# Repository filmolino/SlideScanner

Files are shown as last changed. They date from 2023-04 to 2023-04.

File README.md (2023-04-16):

# Filmolino SlideScanner
The Filmolino SlideScanner is a device that makes it easy to scan slides in magazines fully automated using a modified slide projector and a digital camera. It controls the slide projector and a digital camera using a cable release or an infrared remote control (Nikon, Canon, Pentax, Sony, Olympus, Minolta). New cable releases and IR controls can easyily be added to the software. 
 
Thanks to the [M5StampC3 from M5Stack](https://shop.m5stack.com/collections/m5-controllers/products/fire-iot-development-kit) using a ESP-32 core together with 16M Flash, 8M PSRAM and a built in 3.7V/500mAh Lithium battery it is also possible to use the device without a power supply and remote control the SlideScanner through a web interface over WiFi. The scanner has it's own access point to which you can connect.

The Filmolino SlideScanner is completely open source, so you can easy build your own!

For more info about the project please visit [Filmolino SlideScanner](https://filmolino.com/slidescanner/)

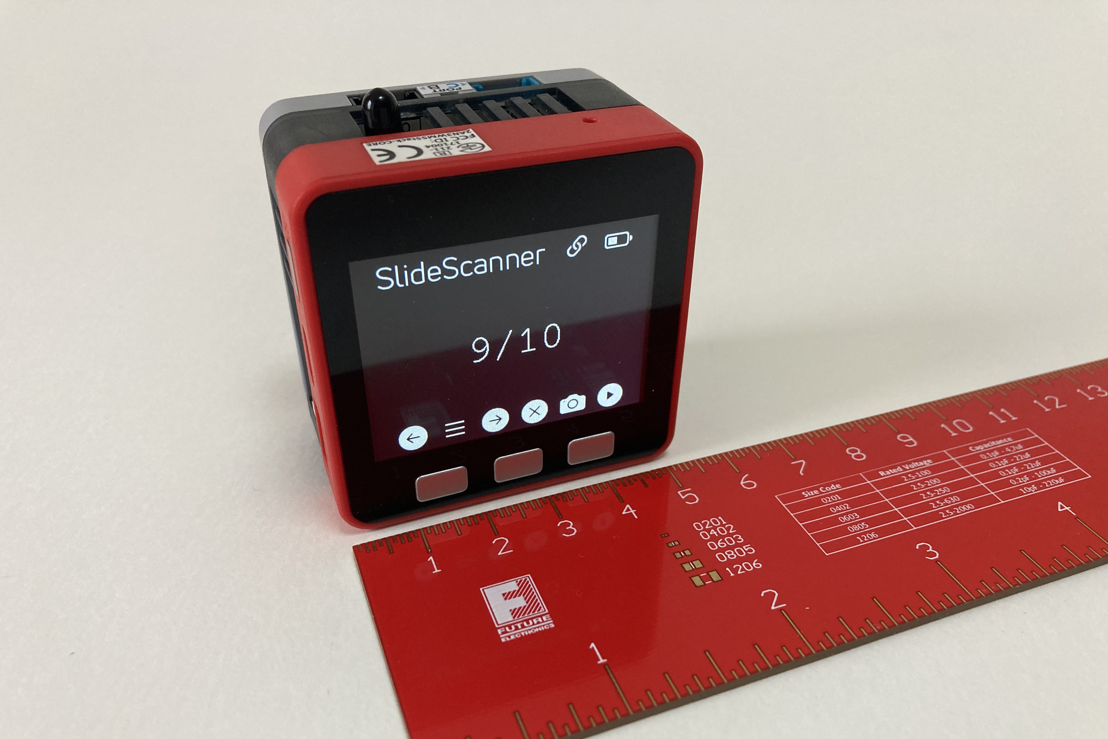
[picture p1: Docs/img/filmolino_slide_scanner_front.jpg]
Front view Front view Filmolino SlideScanner

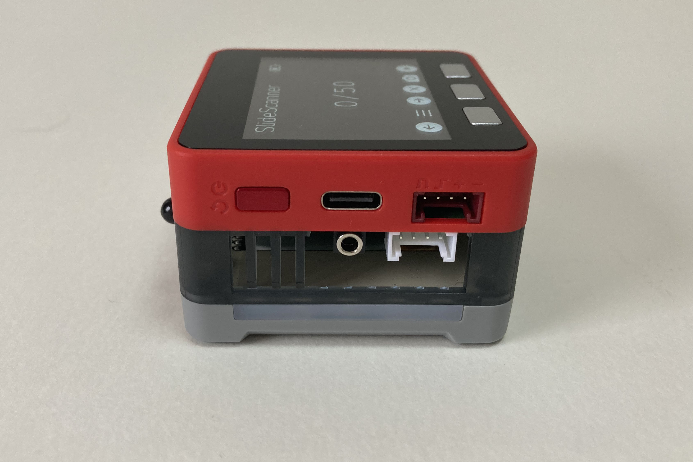
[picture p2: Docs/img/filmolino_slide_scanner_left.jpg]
Left view Left view Filmolino SlideScanner

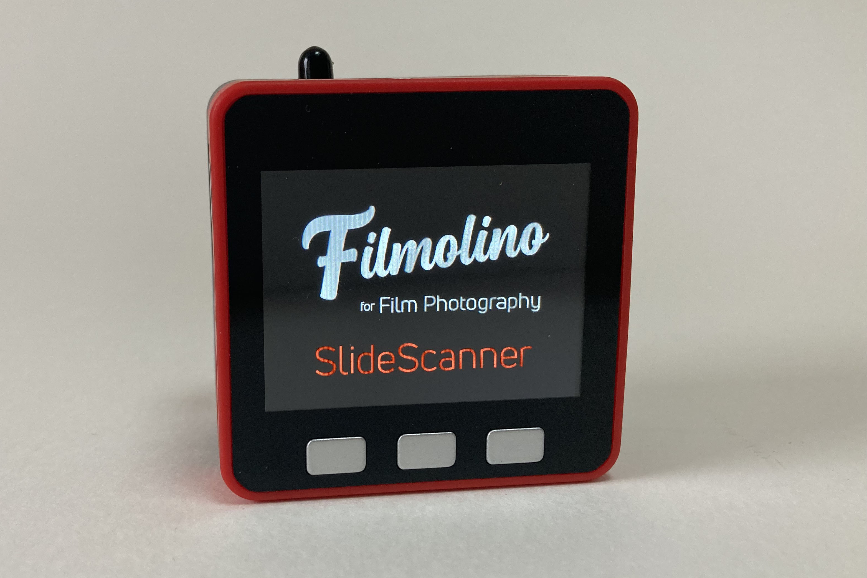
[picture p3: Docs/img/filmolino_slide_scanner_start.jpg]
Left view Left view Filmolino SlideScanner

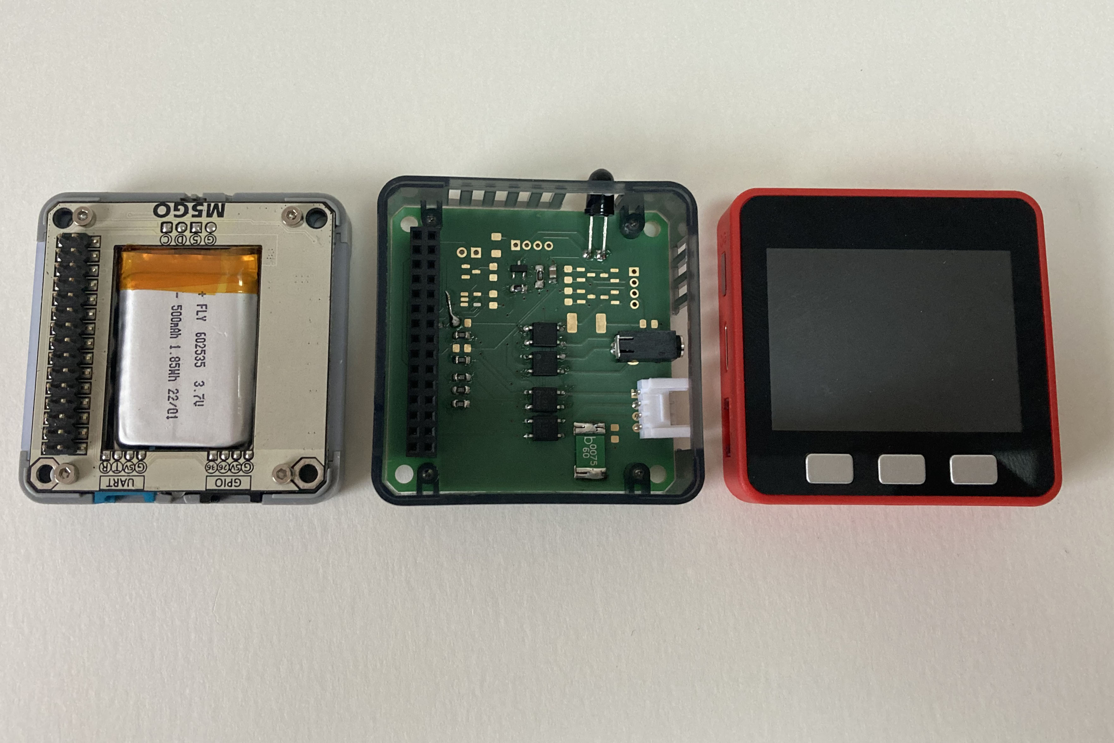
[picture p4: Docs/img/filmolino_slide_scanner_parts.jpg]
Parts view Parts


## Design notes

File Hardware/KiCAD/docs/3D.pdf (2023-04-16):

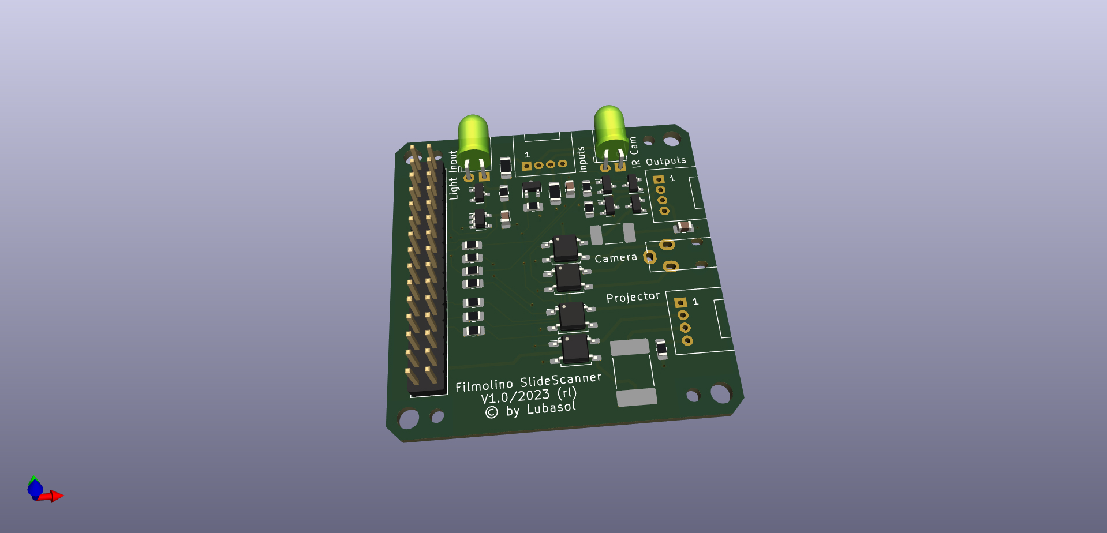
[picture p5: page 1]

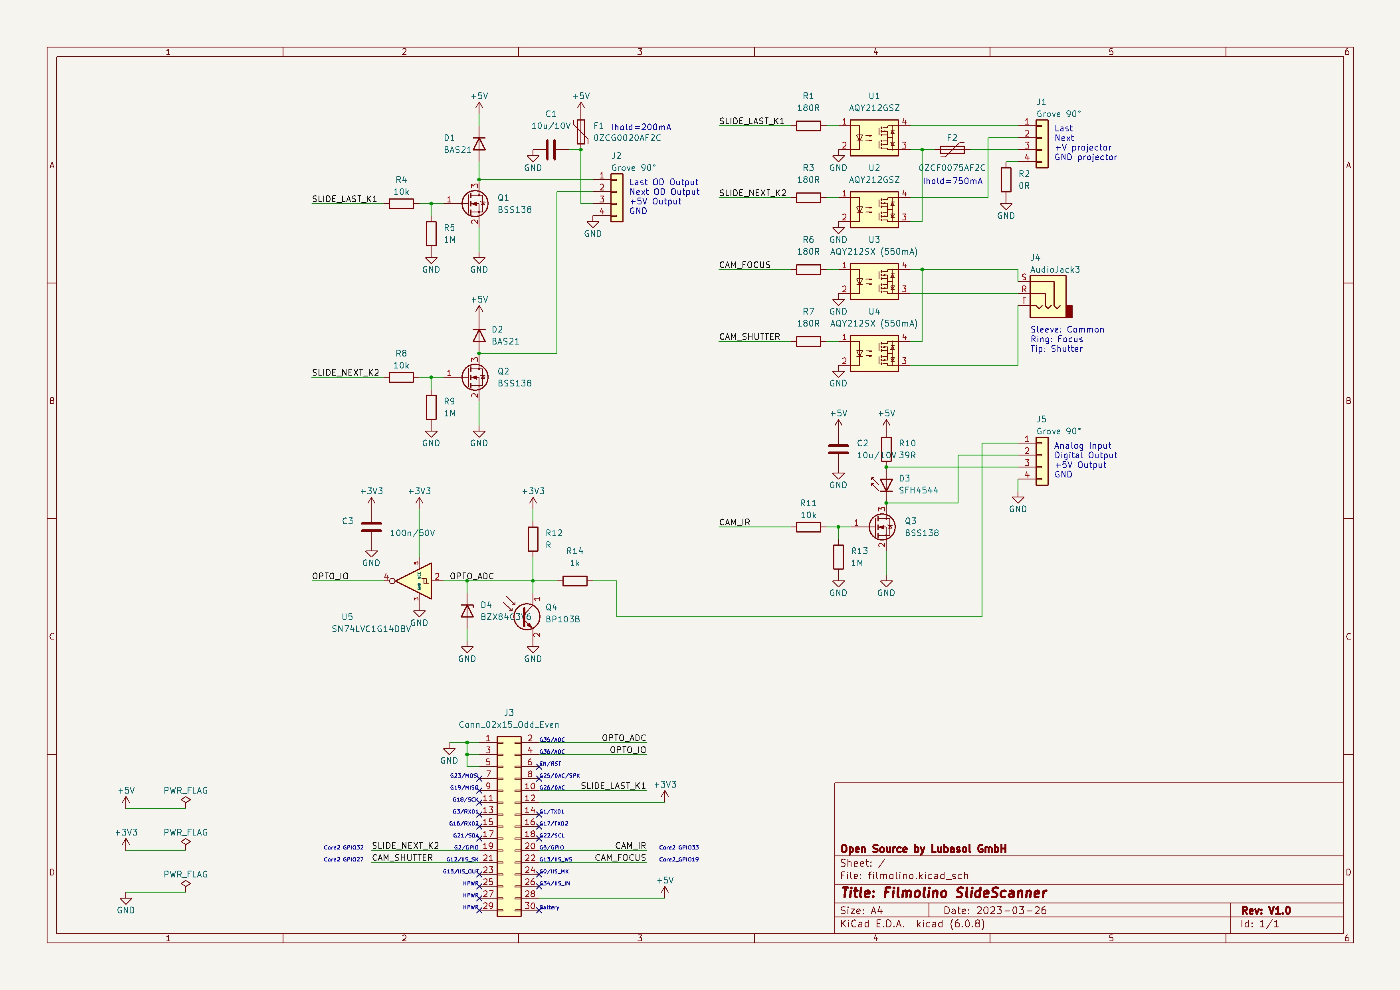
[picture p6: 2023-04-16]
Docs/img/kicad_schematic.jpg

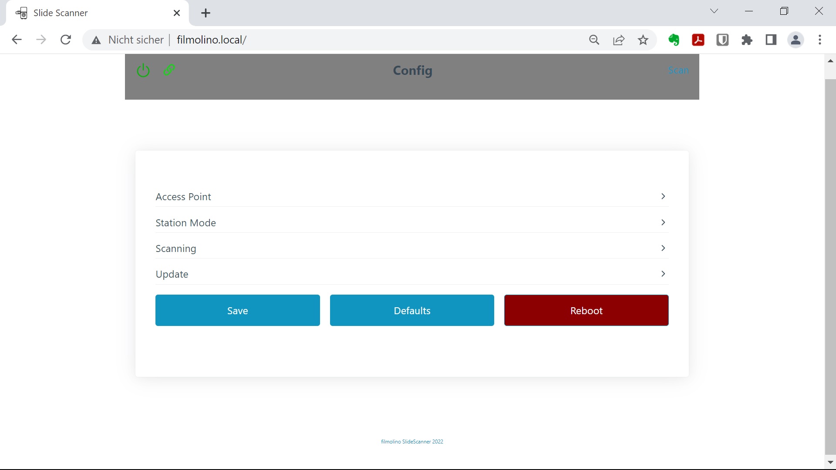
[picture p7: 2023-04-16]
Docs/img/web_config.jpg

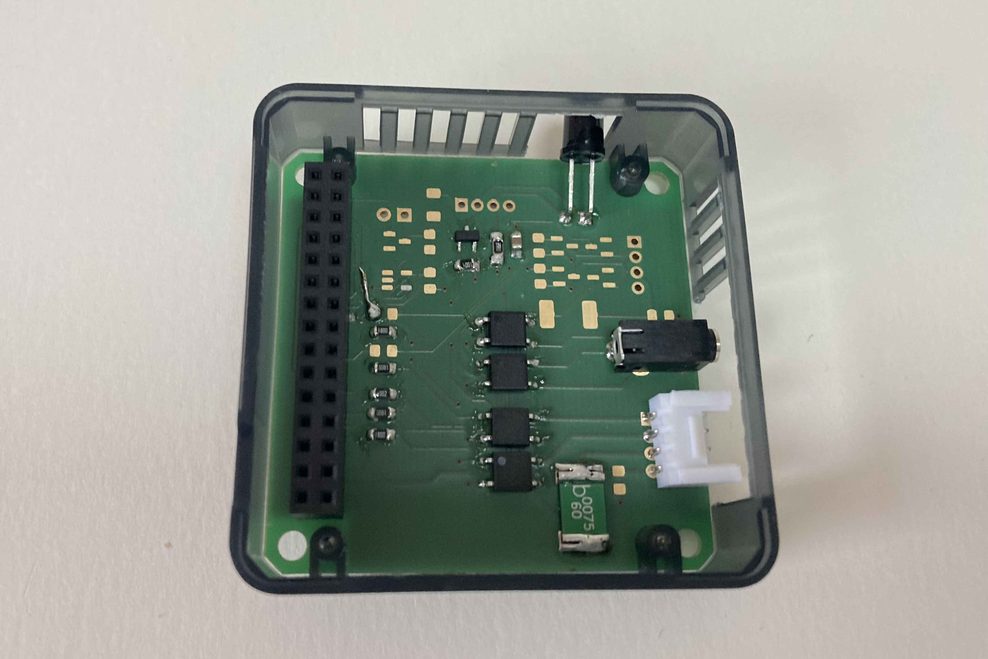
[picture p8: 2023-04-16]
Docs/img/filmolino_slide_scanner_pcb.jpg

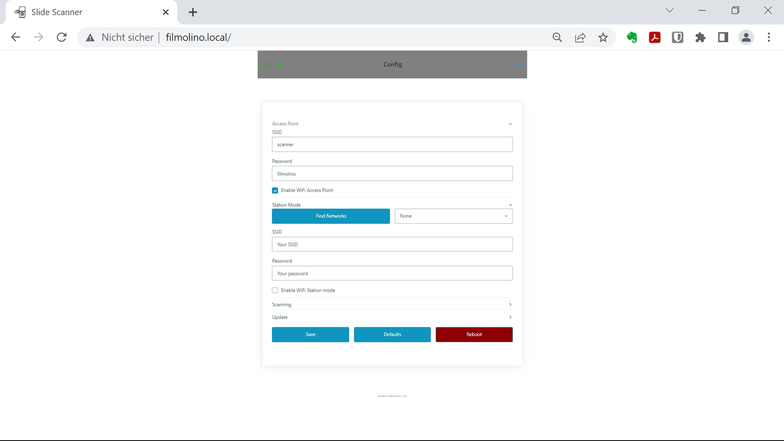
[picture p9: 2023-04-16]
Docs/img/web_config_wifi.jpg

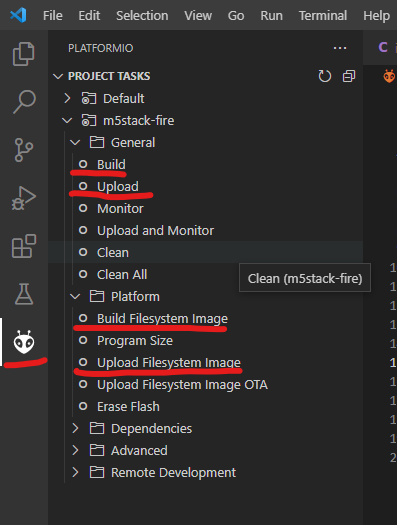
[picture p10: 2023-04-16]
Docs/img/platformio.png

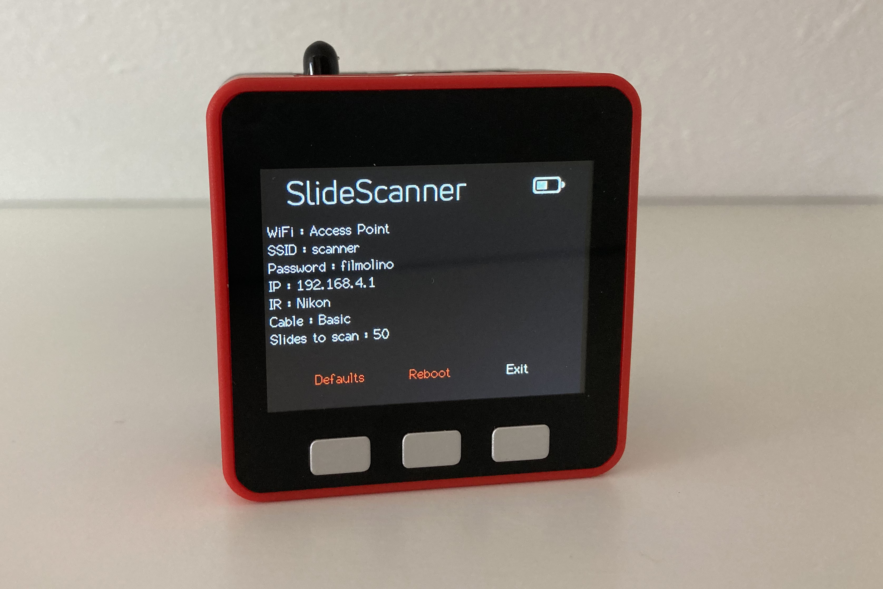
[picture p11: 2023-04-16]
Docs/img/filmolino_slide_scanner_config.jpg

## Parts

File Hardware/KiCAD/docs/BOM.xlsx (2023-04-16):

Id | Designator | Package | Quantity | Designation | Supplier and ref
1 | Q3,Q1,Q2 | SOT-23 | 3 | BSS138
2 | D1,D2 | SOT-23 | 2 | BAS21
3 | U3,U4 | SOP-4_4.4x4.3mm_P2.54mm | 2 | AQY212SX (550mA)
4 | U2,U1 | SOP-4_4.4x4.3mm_P2.54mm | 2 | AQY212GSZ
5 | R9,R5,R13 | R_0805_2012Metric_Pad1.20x1.40mm_HandSolder | 3 | 1M
6 | F1 | BelFuse_0ZCG_Metric_Pad1.78x3.50mm | 1 | 0ZCG0020AF2C
7 | R12 | R_0805_2012Metric_Pad1.20x1.40mm_HandSolder | 1 | R
8 | J4 | Jack_2.5mm_Lumberg_1501_04 | 1 | AudioJack3
9 | D4 | SOT-23 | 1 | BZX84C3V6
10 | J2,J1,J5 | Grove_Con_1x04_2mm_horizontal | 3 | Grove 90Â°
11 | J3 | PinHeader_2x15_P2.54mm_Holes0.75mm_Vertical | 1 | Conn_02x15_Odd_Even
12 | U5 | SOT-23-5 | 1 | SN74LVC1G14DBV
13 | R4,R11,R8 | R_0805_2012Metric_Pad1.20x1.40mm_HandSolder | 3 | 10k
14 | C2,C1 | C_0805_2012Metric_Pad1.18x1.45mm_HandSolder | 2 | 10u/10V
15 | D3 | LED_D5.0mm_Horizontal_O1.27mm_Z3.0mm | 1 | SFH4544
16 | F2 | BelFuse_0ZCF_Metric_Pad2.30x5.60mm | 1 | 0ZCF0075AF2C
17 | R1,R7,R3,R6 | R_0805_2012Metric_Pad1.20x1.40mm_HandSolder | 4 | 180R
18 | R2 | R_0805_2012Metric_Pad1.20x1.40mm_HandSolder | 1 | 0R
19 | Q4 | LED_D5.0mm_Horizontal_O1.27mm_Z3.0mm | 1 | BP103B
20 | C3 | C_0805_2012Metric_Pad1.18x1.45mm_HandSolder | 1 | 100n/50V
21 | R14 | R_1206_3216Metric_Pad1.30x1.75mm_HandSolder | 1 | 1k
22 | R10 | R_1206_3216Metric_Pad1.30x1.75mm_HandSolder | 1 | 39R

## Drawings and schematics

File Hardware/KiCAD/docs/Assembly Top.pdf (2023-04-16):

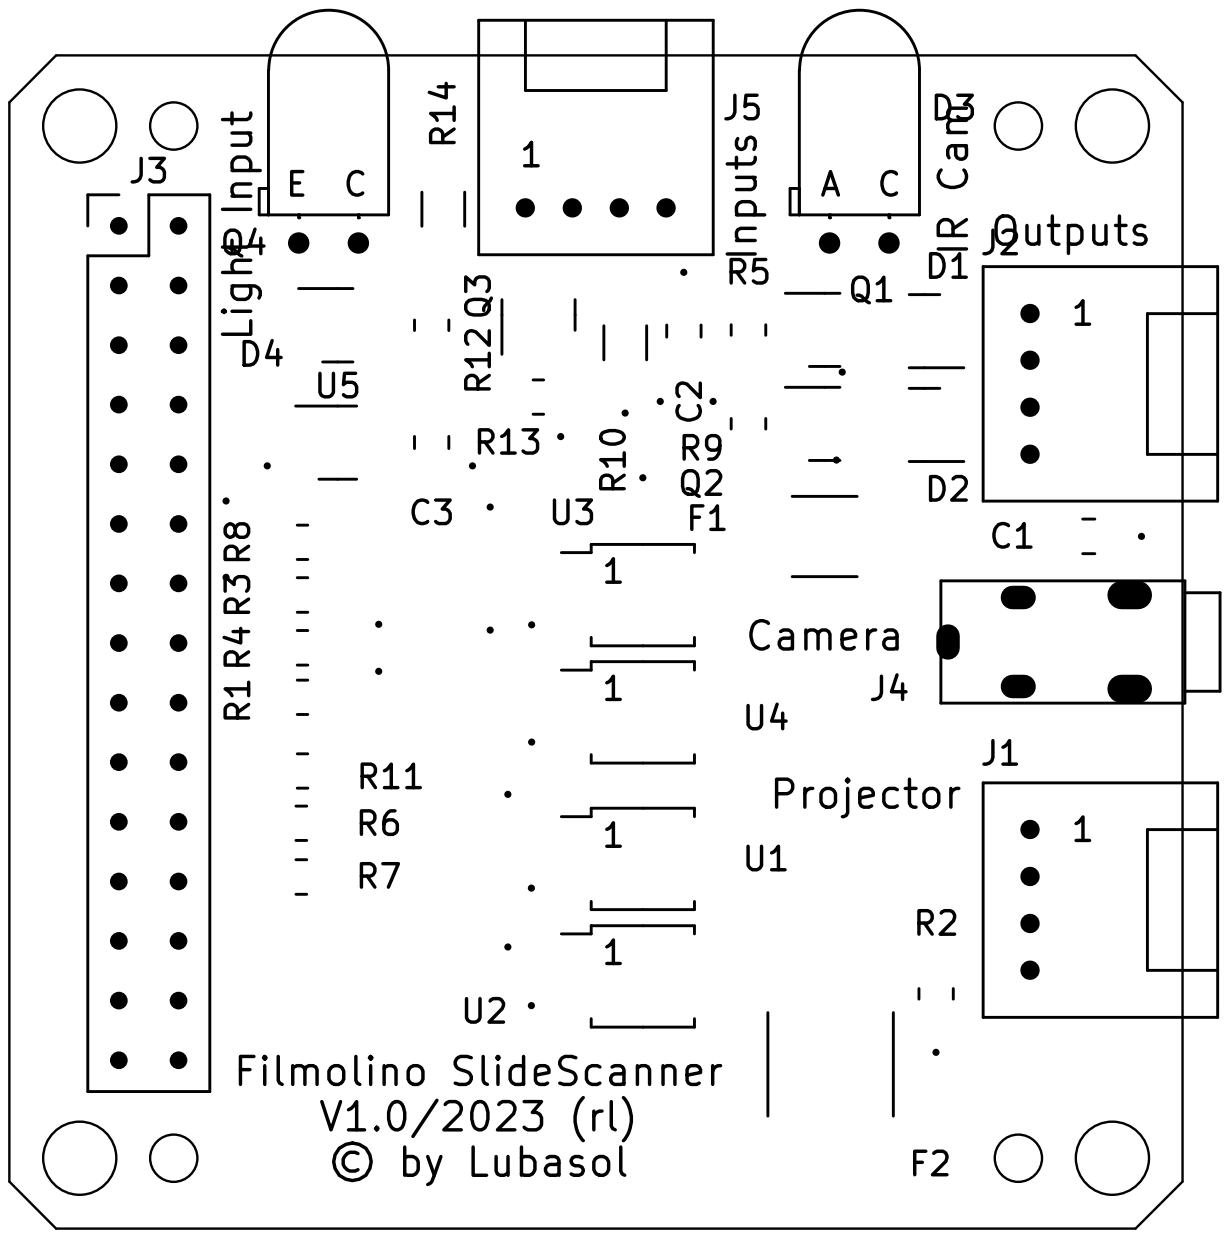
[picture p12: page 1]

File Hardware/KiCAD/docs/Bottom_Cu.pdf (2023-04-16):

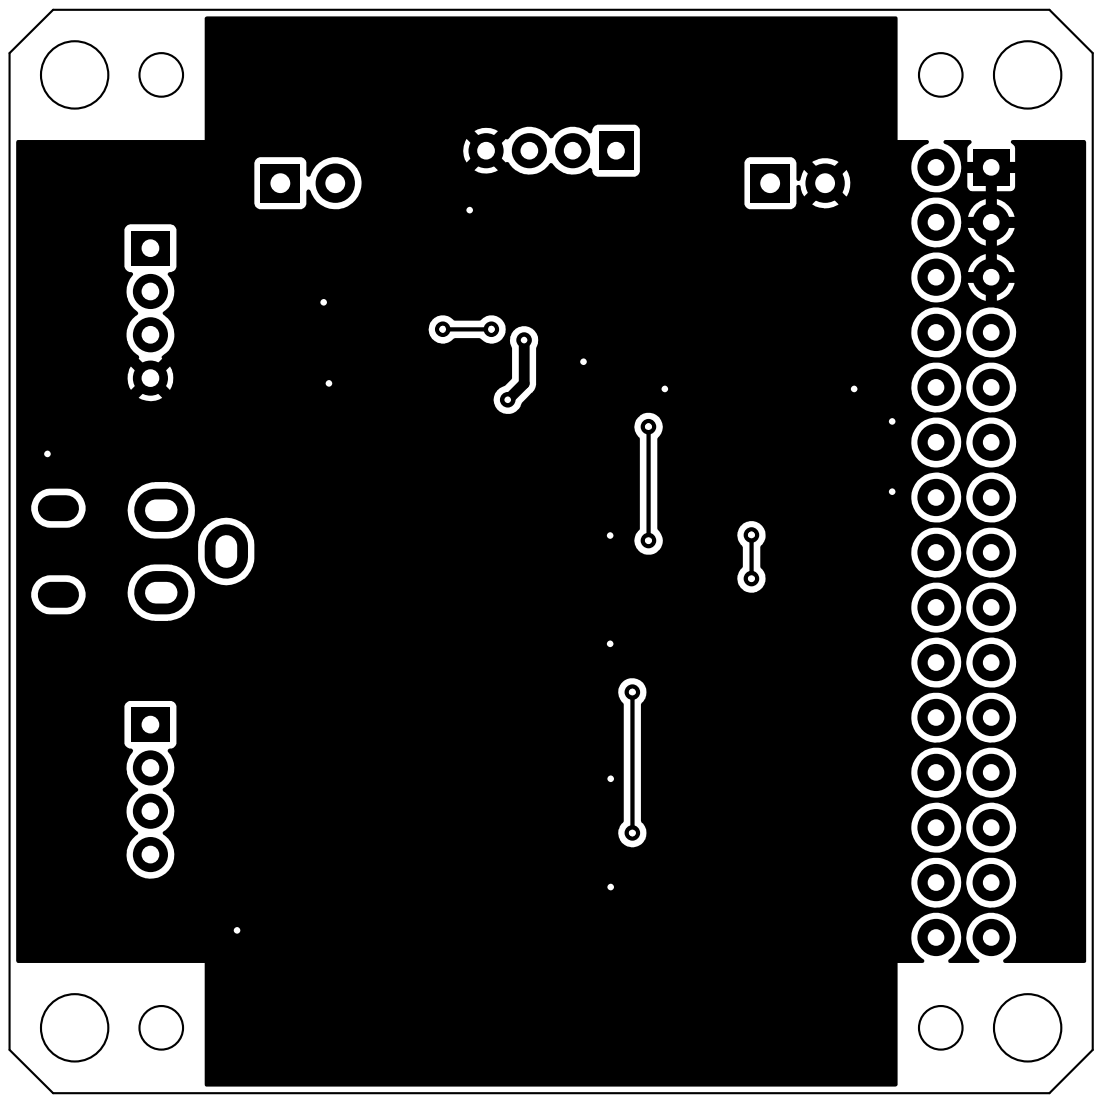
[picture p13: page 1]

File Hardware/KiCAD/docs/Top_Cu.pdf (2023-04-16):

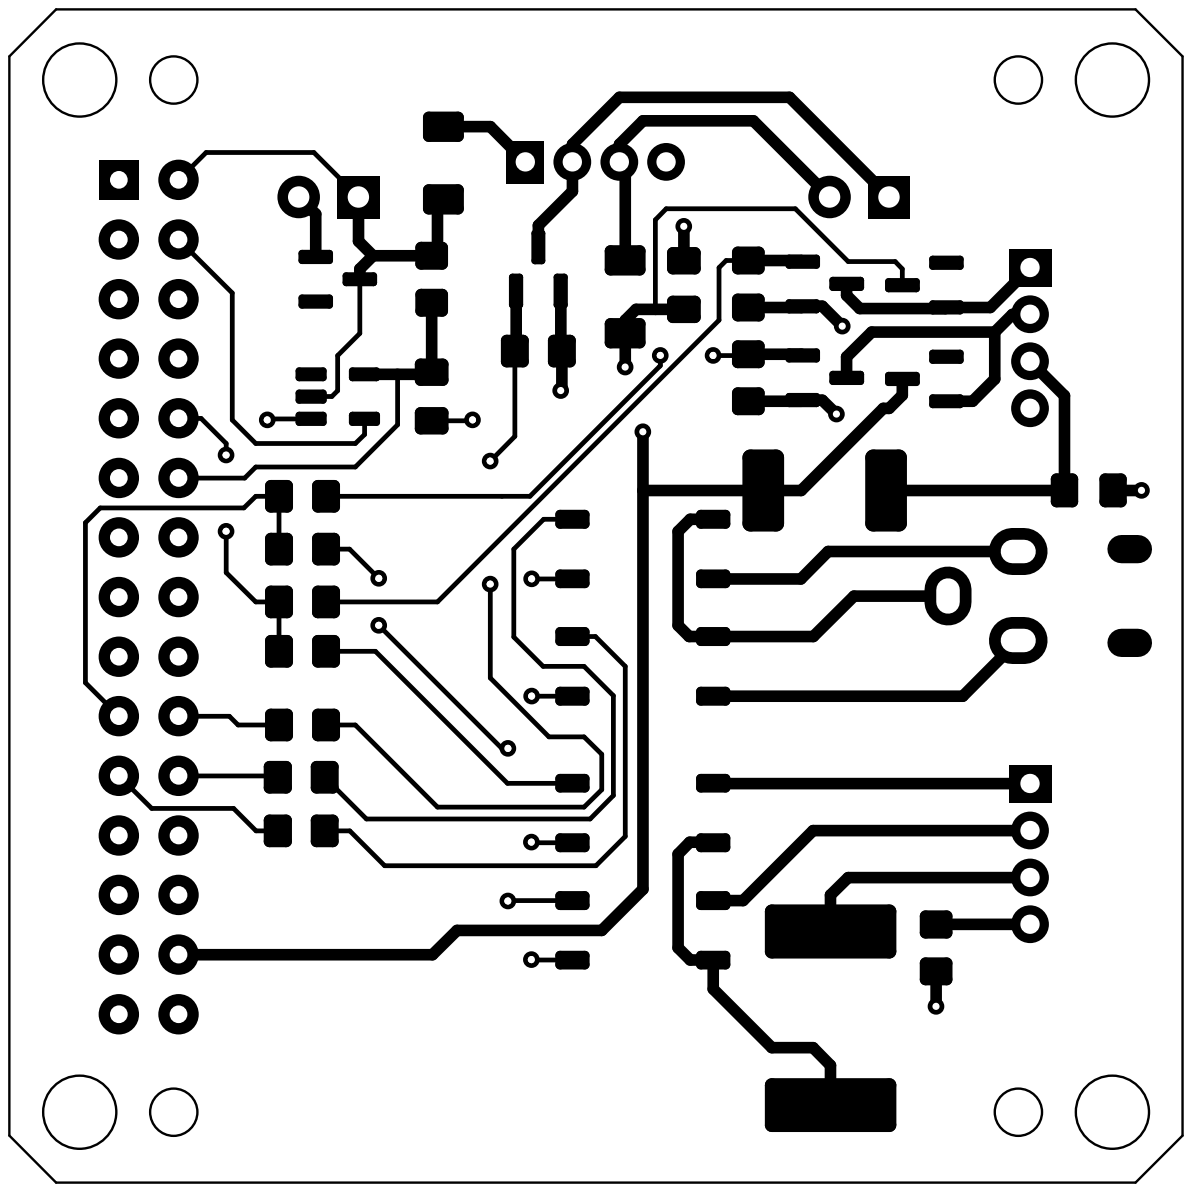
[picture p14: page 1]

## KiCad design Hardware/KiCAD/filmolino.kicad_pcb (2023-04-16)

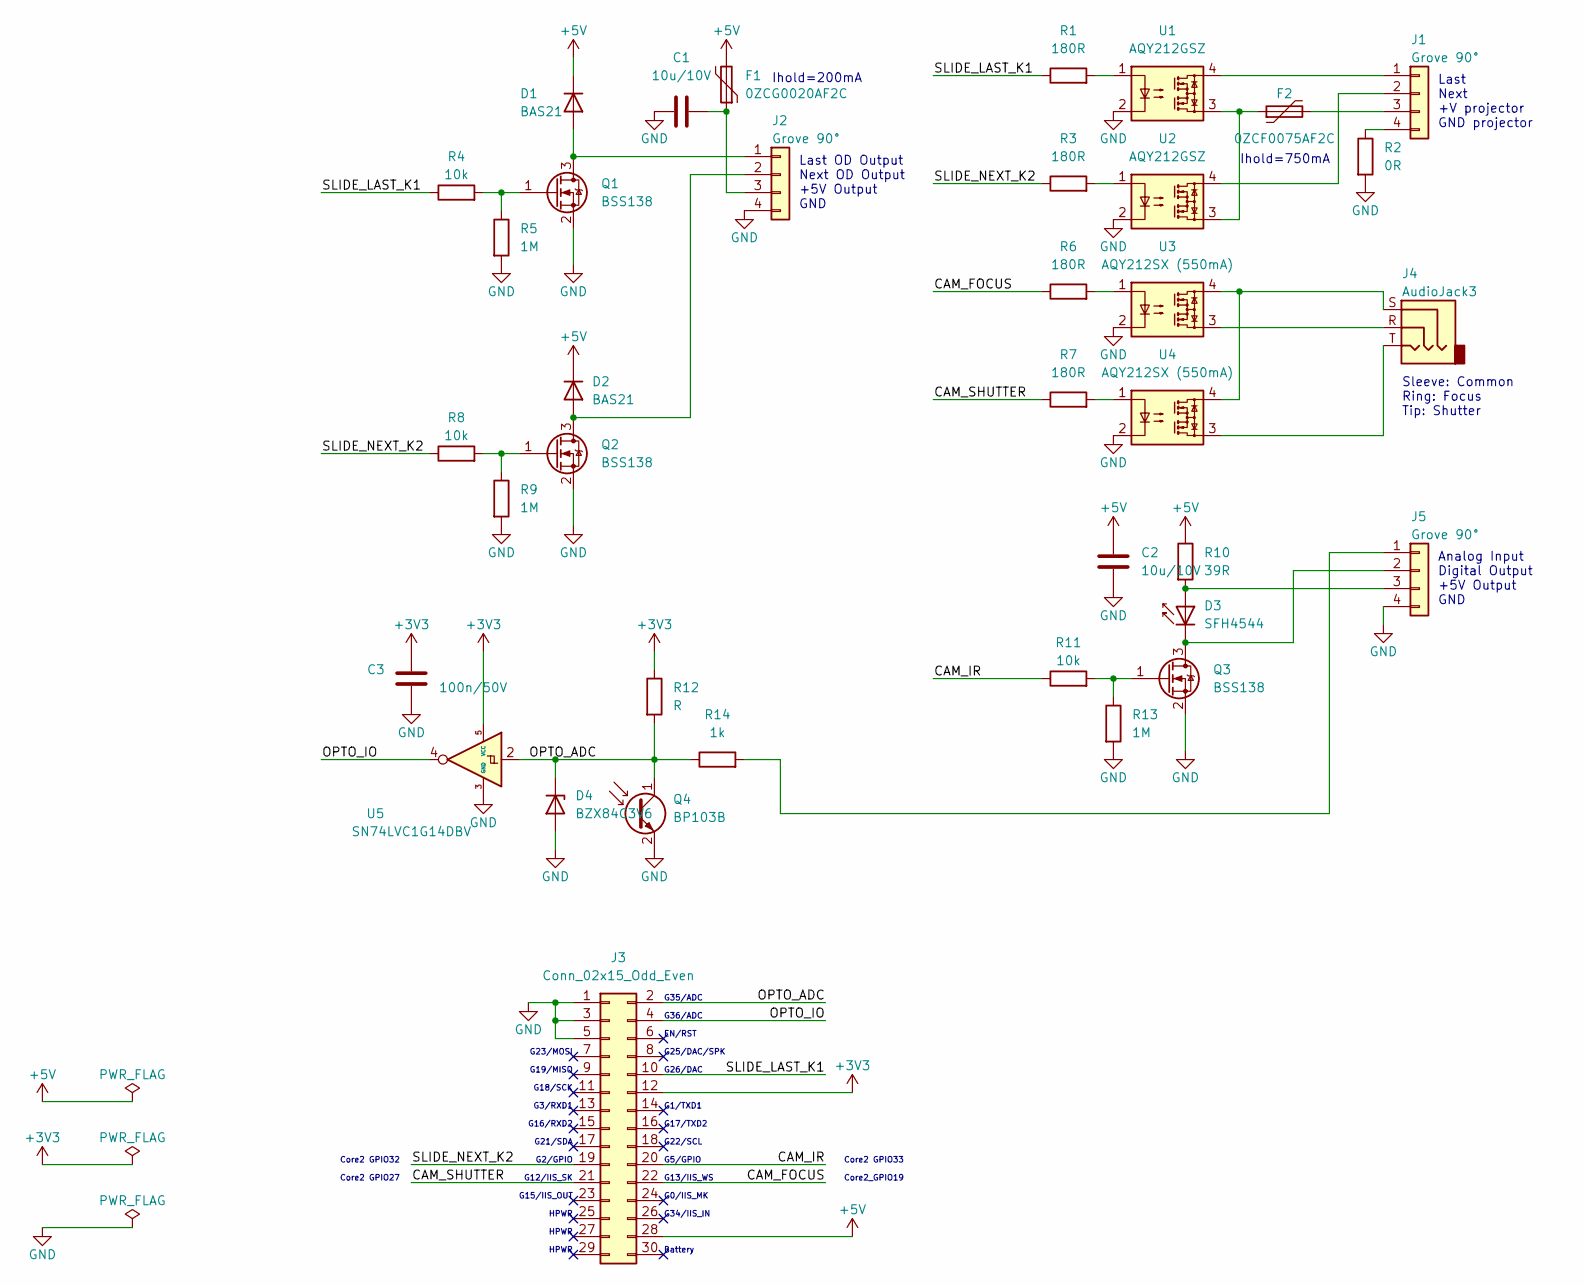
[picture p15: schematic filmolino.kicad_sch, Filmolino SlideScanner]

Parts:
C1, C2: 10u/10V; C_0805_2012Metric_Pad1.18x1.45mm_HandSolder
C3: 100n/50V; C_0805_2012Metric_Pad1.18x1.45mm_HandSolder
D1, D2: BAS21; SOT-23
D3: SFH4544; LED_D5.0mm_Horizontal_O1.27mm_Z3.0mm
D4: BZX84C3V6; SOT-23
F1: 0ZCG0020AF2C; BelFuse_0ZCG_Metric_Pad1.78x3.50mm
F2: 0ZCF0075AF2C; BelFuse_0ZCF_Metric_Pad2.30x5.60mm
J1, J2, J5: Grove 90°; Grove_Con_1x04_2mm_horizontal
J3: Conn_02x15_Odd_Even; PinHeader_2x15_P2.54mm_Holes0.75mm_Vertical
J4: AudioJack3; Jack_2.5mm_Lumberg_1501_04
Q1, Q2, Q3: BSS138; SOT-23
Q4: BP103B; LED_D5.0mm_Horizontal_O1.27mm_Z3.0mm
R1, R3, R6, R7: 180R; R_0805_2012Metric_Pad1.20x1.40mm_HandSolder
R2: 0R; R_0805_2012Metric_Pad1.20x1.40mm_HandSolder
R4, R8, R11: 10k; R_0805_2012Metric_Pad1.20x1.40mm_HandSolder
R5, R9, R13: 1M; R_0805_2012Metric_Pad1.20x1.40mm_HandSolder
R10: 39R; R_1206_3216Metric_Pad1.30x1.75mm_HandSolder
R12: R; R_0805_2012Metric_Pad1.20x1.40mm_HandSolder
R14: 1k; R_1206_3216Metric_Pad1.30x1.75mm_HandSolder
U1, U2: AQY212GSZ; SOP-4_4.4x4.3mm_P2.54mm
U3, U4: AQY212SX (550mA); SOP-4_4.4x4.3mm_P2.54mm
U5: SN74LVC1G14DBV; SOT-23-5

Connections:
+3V3: C3.1, J3.12, R12.1, U5.5 (VCC)
+5V: C2.1, D1.3 (K), D2.3 (K), F1.2, J3.28, R10.1
/CAM_FOCUS: J3.22, R6.1
/CAM_IR: J3.20, R11.1
/CAM_SHUTTER: J3.21, R7.1
/OPTO_ADC: D4.3 (K), J3.2, Q4.1 (C), R12.2, R14.1, U5.2
/OPTO_IO: J3.4, U5.4
/SLIDE_LAST_K1: J3.10, R1.1, R4.1
/SLIDE_NEXT_K2: J3.19, R3.1, R8.1
GND: C1.2, C2.2, C3.2, D4.1 (A), J2.4, J3.1, J3.3, J3.5, J5.4, Q1.2 (S), Q2.2 (S), Q3.2 (S), Q4.2 (E), R2.2, R5.2, R9.2, R13.2, U1.2, U2.2, U3.2, U4.2, U5.3 (GND)
unnamed: C1.1, F1.1, J2.3
unnamed: D1.1 (A), J2.1, Q1.3 (D)
unnamed: D2.1 (A), J2.2, Q2.3 (D)
unnamed: D3.1 (K), J5.2, Q3.3 (D)
unnamed: D3.2 (A), J5.3, R10.2
unnamed: F2.1, U1.3, U2.3
unnamed: F2.2, J1.3
unnamed: J1.1, U1.4
unnamed: J1.2, U2.4
unnamed: J1.4, R2.1
unnamed: J4.R, U3.3
unnamed: J4.S, U3.4, U4.4
unnamed: J4.T, U4.3
unnamed: J5.1, R14.2
unnamed: Q1.1 (G), R4.2, R5.1
unnamed: Q2.1 (G), R8.2, R9.1
unnamed: Q3.1 (G), R11.2, R13.1
unnamed: R1.2, U1.1
unnamed: R3.2, U2.1
unnamed: R6.2, U3.1
unnamed: R7.2, U4.1

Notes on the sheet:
Core2 GPIO27
Ihold=750mA
G3/RXD1
Last OD Output Next OD Output +5V Output GND
EN/RST
G16/RXD2
G12/IIS_SK
G36/ADC
HPWR
Battery
G17/TXD2
G22/SCL
Sleeve: Common Ring: Focus Tip: Shutter
Core2 GPIO33
G35/ADC
G18/SCK
Last Next +V projector GND projector
Ihold=200mA
G23/MOSI
G26/DAC
G1/TXD1
G13/IIS_WS
G19/MISO
Core2 GPIO32
G15/IIS_OUT
G0/IIS_MK
G25/DAC/SPK
G34/IIS_IN
Analog Input Digital Output +5V Output GND
G5/GPIO
G2/GPIO
G21/SDA
Core2_GPIO19

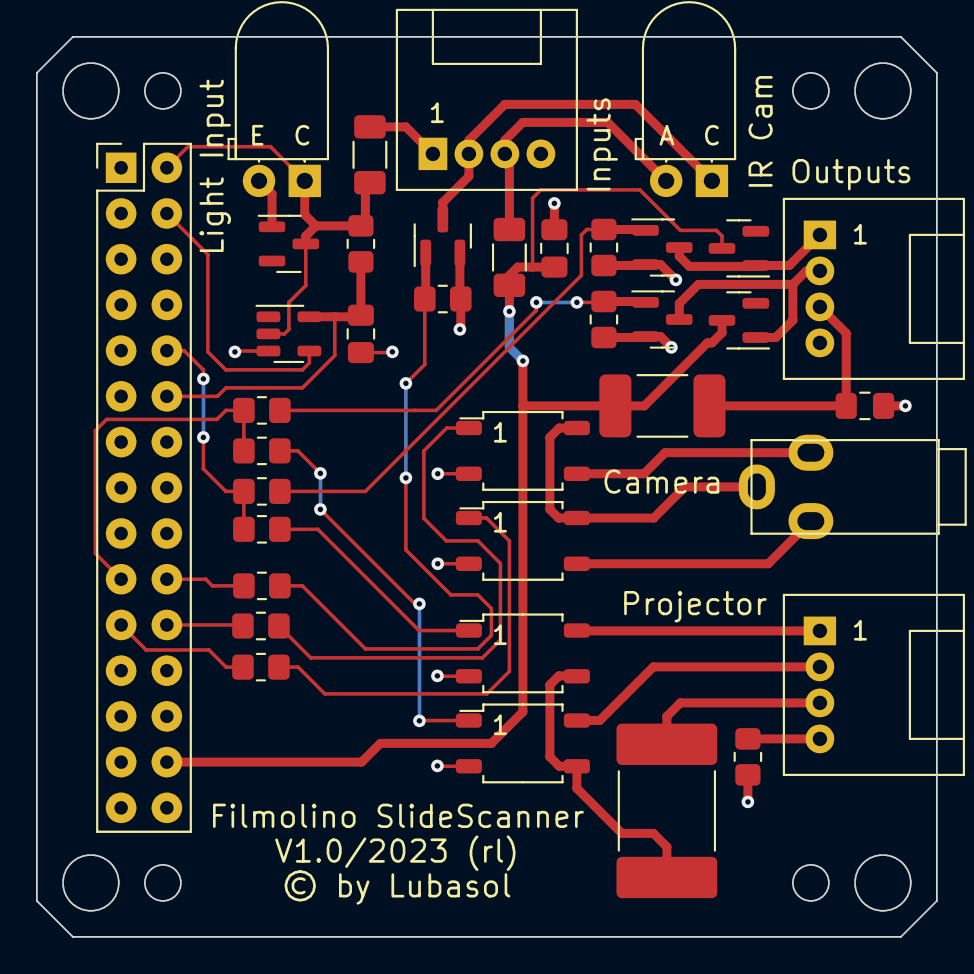
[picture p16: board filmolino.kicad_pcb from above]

Board: 2 copper layers, 50.0 x 50.0 mm, 37 parts (0 on the bottom side), 31 nets.

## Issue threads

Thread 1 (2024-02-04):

Wifi Settings: Unable to use AP Name or password longer than 13 characters

softcat, 2024-02-04:
First of all thank you for the great project, I built one using your instructions and it works nearly perfectly.

There is one issue which took some time to figure out:

After connecting to the initial AP "scanner" I tried to enter the credentials for my home wlan which failed after saving the settings.

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

This happens everytime when entering a string longer than 13 characters  in any SSID or password field in AP or stationary mode.

When looking at the debug console

```
Power canControl OK
display_task created
SPIFFS init ok
config file not found...
Config init OK
current_seq = 1
cable_release_task created
control_task created
Starting STA...HTTP /index.hmtl
WebSocket EVENTWebSocket client #1 connected from 192.168.0.133
WebSocket EVENTWebSocket dataws[/ws][1] text-message[16]: getCableRelNames
[WS] getCableRelNames
[WS] AFTER getCableRelNames
WebSocket EVENTWebSocket dataws[/ws][1] text-message[13]: getIrRelNames
[WS] getIrRelNames
WebSocket EVENTWebSocket dataws[/ws][1] text-message[10]: getWiFiCfg
[WS] getWiFiCfg
WebSocket EVENTWebSocket dataws[/ws][1] text-message[10]: getScanCfg
[WS] getScanCfg
WebSocket EVENTWebSocket dataws[/ws][1] text-message[52]: setWiFiCfg,scanner,filmolino,MyAP,12345678901234,0,1
[WS] setWiFiCfg
ap_ssid = scanner
ap_ssid = filmolino
sta_ssid = MyAP
sta_password = D��?␏
ap = 0
sta = 1
WebSocket EVENTWebSocket dataws[/ws][1] text-message[35]: setScanCfg,2000,250,1500,50,1,5,1,1
[WS] setScanCfg
delay_slide_change = 2000
time_slide_change_pulse = 250
delay_slide_scan = 1500
slides_to_scan = 50
ir = 1
ir_selected_code = 5
cable = 1
cable_selected_code = 1
WebSocket EVENTWebSocket dataws[/ws][1] text-message[10]: saveConfig
[WS] saveConfig
WebSocket EVENTWebSocket dataws[/ws][1] text-message[10]: getWiFiCfg
[WS] getWiFiCfg
WebSocket EVENTWebSocket dataws[/ws][1] text-message[10]: getScanCfg
[WS] getScanCfg
WebSocket EVENTWebSocket client #1 disconnected
```

I can see that the password "12345678901234" is transmitted to the Filmolino but when beeing processed changes to something glibberish like `D��?␏`. One byte less works fine.

Unfortunately I'm not into C programming and could no figure out the cause myself....

For a workaround I setup a dedicated SSID with a short password for the filmolino and of course it also works offline...

Many thanks!

filmolino, 2024-02-05:
Hi SoftCat thanks for your reply, I will check it soon...

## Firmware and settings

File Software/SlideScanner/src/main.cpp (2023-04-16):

#include <Arduino.h>
#include <M5Stack.h>
#include "SPIFFS.h"
#include "ir_release.h"
#include "control.h"
#include "config.h"
#include "project.h"

// Display
Display display;

// Config
Config settings(CONFIG_FILE_NAME);

// Camera releases
IrRelease ir_release;
CableRelease cable_release;

// Control
Control control;
QueueHandle_t control_evt_queue = NULL;

// Cable Release
QueueHandle_t cable_release_evt_queue = NULL;

// Wifi
WiFiManager wifimanager;

// Web
Webmanager webmanager;

void control_task(void *param) {
  control_evt_t evt;

  Serial.println("control_task created");

  while (1) {
    if (xQueueReceive(control_evt_queue, (void*) &evt, 10)) {      
      control.sm(evt);
    }
  }
}


void cable_release_task(void *param) {
  cable_release_evt_t evt;

  Serial.println("cable_release_task created");

  while (1) {
    if (xQueueReceive(cable_release_evt_queue, (void*) &evt, 10)) {
      Serial.println("cable_release_task QUEUE event"); 
      cable_release.sm(evt);
    }
  }
}



void display_task(void *param) {
  Serial.println("display_task created");

  while (1) {
    display.update_header();
    vTaskDelay(2000/portTICK_PERIOD_MS);
  }
}


void setup() {
  Serial.begin(115200);

  // M5Stack 
  M5.begin(); 
  M5.Power.begin();
  if (M5.Power.canControl()) {
    Serial.println("Power canControl OK");
  } else {
    Serial.println("Power canControl ERROR");
  }

  // Display
  display.begin();
  xTaskCreate(display_task, "display_task", 2048, NULL, 10, NULL);

  // SPIFFS
  if(!SPIFFS.begin(true)){
    Serial.println("An Error has occurred while mounting SPIFFS");
    return;
  }
  else {
    Serial.println("SPIFFS init ok");
  }

  // Get config data
  settings.begin();
  display.update_main_scan(0, settings.get_slides_to_scan());
  
  // IR Release
  uint8_t code = settings.get_ir_selected_code();
  uint8_t divider = settings.get_ir_divider(code);
  uint32_t freq = settings.get_ir_freq(code);
  ir_release.begin(GPIO_IR_RELEASE, RMT_CHANNEL_0, divider, freq);

  // Cable Release
  cable_release.begin(GPIO_CABLE_RELEASE_SHUTTER, GPIO_CABLE_RELEASE_FOCUS);
  settings.set_cable_release();
  cable_release_evt_queue = xQueueCreate(10, sizeof(cable_release_evt_t));
  xTaskCreate(cable_release_task, "cable_release_task", 2048, NULL, 10, NULL);
  
  // Control State Machine
  control.begin(GPIO_RELAY_LAST, GPIO_RELAY_NEXT);
  
  // Control Task
  control_evt_queue = xQueueCreate(10, sizeof(control_evt_t));
  xTaskCreate(control_task, "control_task", 2048, NULL, 10, NULL);   

  // WiFi Router
  wifimanager.begin();

  // WebServer
  webmanager.begin();
}

void loop() {
  static long lastBtnMillis = 0;
  long currentMillis = millis();

  // Buttons
  if (currentMillis - lastBtnMillis > BTN_PERIOD) {
    lastBtnMillis = millis();
    display.buttons();
  }

  // WiFiManager
  wifimanager.loop();
}

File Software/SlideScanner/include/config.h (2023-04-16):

#ifndef __CONFIG_H
#define __CONFIG_H 

#include "Arduino.h"
#include "cable_release.h"
#include "ir_release.h"

#define CONFIG_FILE_NAME "/config.cfg"

#define CONFIG_SCANNER_NAME                       "filmolino"

#define CONFIG_SCANNER_AP_SSID                    "scanner"
#define CONFIG_SCANNER_AP_PASSWORD                "filmolino"
#define CONFIG_SCANNER_AP_ENABLED                 true
#define CONFIG_SCANNER_AP_PARA_MAX_LENGTH         64

#define CONFIG_SCANNER_STA_SSID                   "Your SSID"
#define CONFIG_SCANNER_STA_PASSWORD               "Your password"
#define CONFIG_SCANNER_STA_ENABLED                false
#define CONFIG_SCANNER_STA_PARA_MAX_LENGTH        64

#define CONFIG_DEFAULT_SLIDE_CHANGE_TIME          2000      /* 2s time to change the slide */
#define CONFIG_DEFAULT_SLIDE_CHANGE_PULSE_TIME    250       /* 0.25s pulse time for slide change */
#define CONFIG_DEFAULT_SLIDE_SCAN_TIME            1500      /* 1.5s time to scan/capture the slide */
#define CONFIG_DEFAULT_SLIDES_TO_SCAN             50        /* Slides to scan (slides in magazine) */

#define CONFIG_DEFAULT_IR_ENABLED                 true      /* IR release active */
#define CONFIG_DEFAULT_IR_SELECTED_CODE           5         /* Selected IR release code 3 = NIKON [1..32] */
#define CONFIG_DEFAULT_CABLE_ENABLED              true      /* Cable release active */
#define CONFIG_DEFAULT_CABLE_SELECTED_CODE        1         /* Selected cable release code 1 = BASIC [1..32] */



typedef struct {
  String ap_ssid;                   /* Access Point Settings */
  String ap_password;
  String sta_ssid;                  /* Station Settings */
  String sta_password;
  bool ap;                            /* true if access point is active */
  bool sta;                           /* true if station mode is active */
} config_wifi_t; 


typedef struct {
  uint32_t delay_slide_change;        /* Delay in ms */
  uint32_t time_slide_change_pulse;   /* pulse time in ms */
  uint32_t delay_slide_scan;          /* Delay in ms */
  uint8_t slides_to_scan;             /* Slides to scan */
  bool ir;                            /* true if active */
  uint8_t ir_selected_code;
  bool cable;                         /* true if active */
  uint8_t cable_selected_code;
} config_control_t;

typedef struct {
  const ir_release_seq_t * ir_codes[IR_RELEASE_CODES_SIZE];
  const cable_release_seq_t * cable_codes[CABLE_RELEASE_CODES_SIZE];
} config_release_t;

typedef struct {
  config_wifi_t     wifi;
  config_control_t  control;
  config_release_t  release;
} config_scanner_t;



class Config {
  public:
    // Constructor
    Config(String filename);

    // 
    void begin();
    size_t read();
    size_t write();
    bool remove();
    void load_defaults();
    config_wifi_t get_wifi();
    void set_wifi(config_wifi_t data);
    uint32_t get_delay_slide_change();
    uint32_t get_delay_slide_scan();
    uint8_t get_slides_to_scan();
    uint32_t get_time_slide_change_pulse();
    bool get_cable_active();
    uint8_t get_cable_selected_code();
    String get_cable_name(uint8_t code);
    bool get_ir_active();
    uint8_t get_ir_divider(uint8_t code);
    uint32_t get_ir_freq(uint8_t code);
    uint8_t get_ir_selected_code();
    String get_ir_name(uint8_t code);
    rmt_item32_t *get_ir_seq();
    void set_cable_release();

    void get_csv_cfg_wifi(char *csv);
    void set_csv_cfg_wifi(char *csv);

    void get_csv_cfg_scanner(char *csv);
    void set_csv_cfg_scanner(char *csv);

    void get_csv_cable_release_names(char *csv, uint32_t bufferSize);
    void get_csv_ir_release_names(char *csv , uint32_t bufferSize);

  private:
    String filename = "";
    config_scanner_t settings;

  };

#endif

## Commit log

2023-04-16 First Release
    [BOM.xlsx, filmolino.csv, filmolino.kicad_pcb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]
2023-05-01 Update filmolino.kicad_sch
    PCB thichkness and M5Stack module frame added.
    [filmolino.kicad_sch]
2023-05-01 Update filmolino.kicad_sch
    Schematic style corrections.
    [filmolino.kicad_sch]

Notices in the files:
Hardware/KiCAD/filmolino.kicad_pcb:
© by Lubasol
